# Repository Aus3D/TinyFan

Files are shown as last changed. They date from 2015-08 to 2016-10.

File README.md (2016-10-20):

# TinyFan

TinyFan is an fan expansion board for the RAMPS 3D printer control board. It allows control of two additional fans through pins D6 and D11.

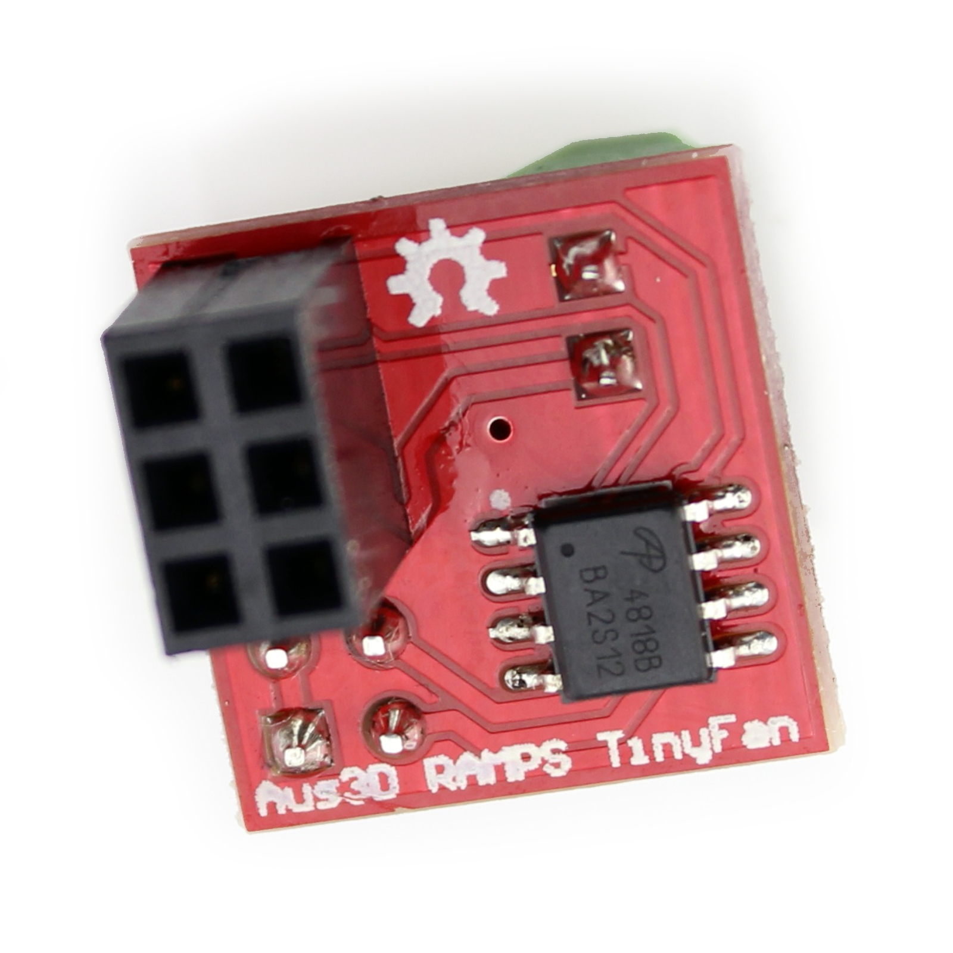
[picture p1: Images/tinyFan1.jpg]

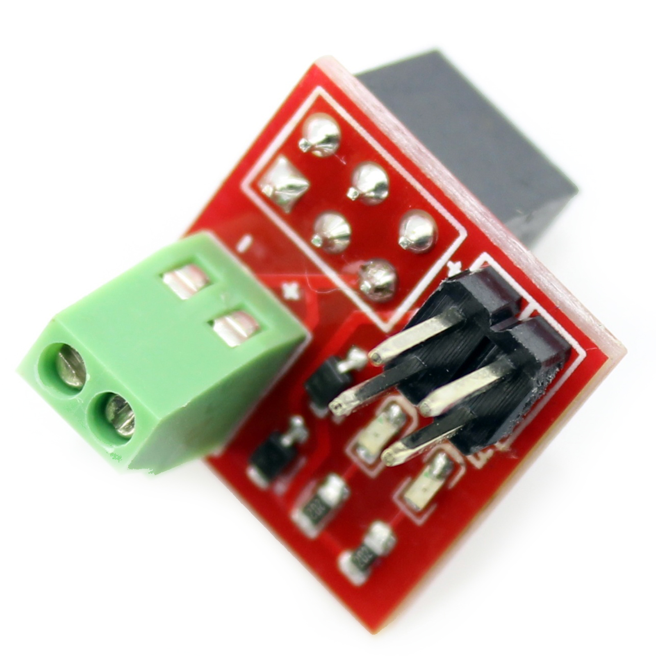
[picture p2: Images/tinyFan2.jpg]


TinyFan is designed to be easy to install. It plugs directly into RAMPS - no soldering is required. A screw terminal allows for connection to 12/24V, so two short wires can be run from RAMPS power input screw terminals to the TinyFan board. This also allows TinyFan to operate at a different voltage to the main power supplied to RAMPS.

Standard .1" pin headers are used for fan connections.

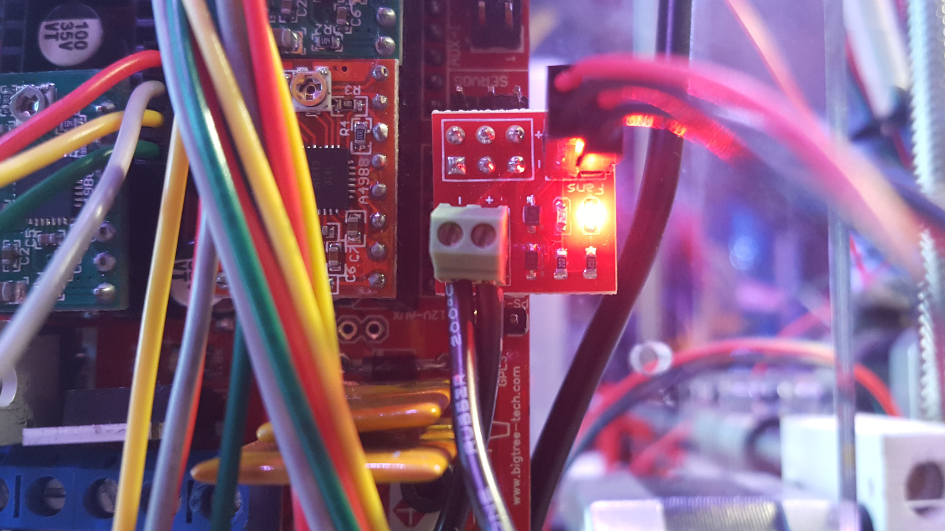
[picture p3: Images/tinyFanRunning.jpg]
TinyFan Running


For more information on TinyFan, including a guide for Marlin firmware configuration, check the [Aus3D Wiki](http://wiki.aus3d.com.au/index.php?title=TinyFan).

TinyFan is open source, and licensed under the GPL V3. TinyFan was designed in Altium Designer, which may make it difficult for some to access - gerber files (for manufacturing) and PDF files (for schematic) have been included to attempt to address this.

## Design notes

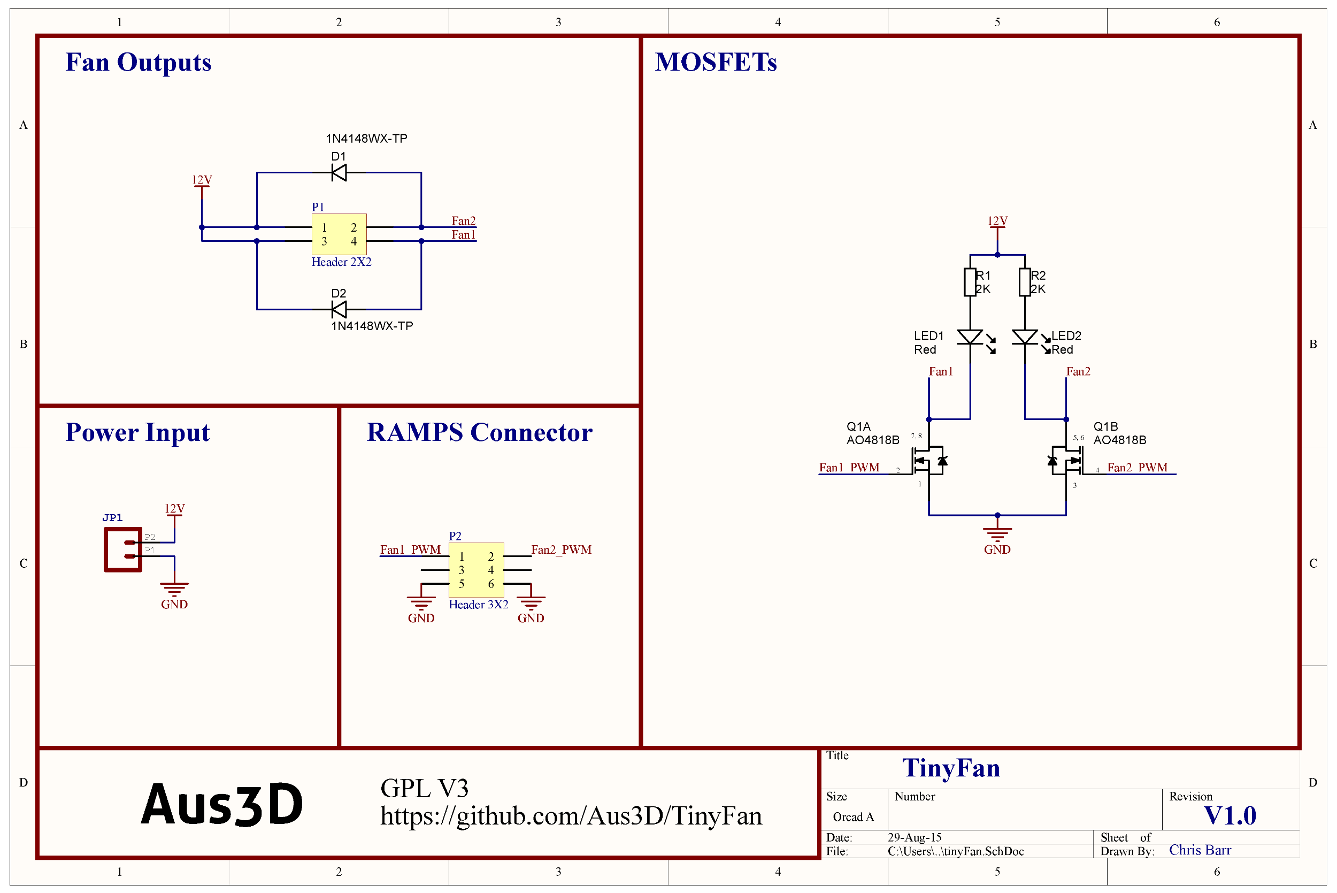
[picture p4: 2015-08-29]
Images/schematic.png

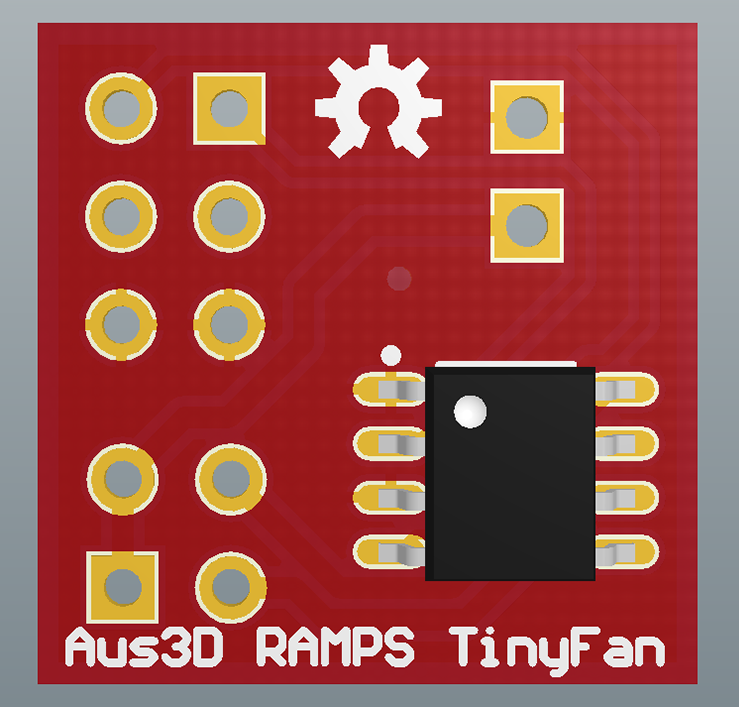
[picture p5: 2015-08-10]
Images/preview2.PNG

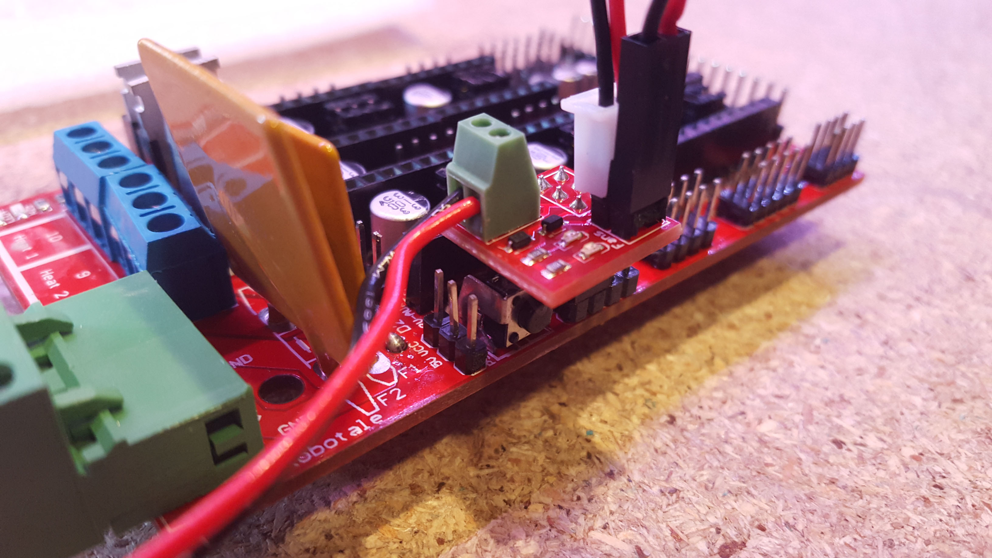
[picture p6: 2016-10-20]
Images/tinyFanConnected2.jpg

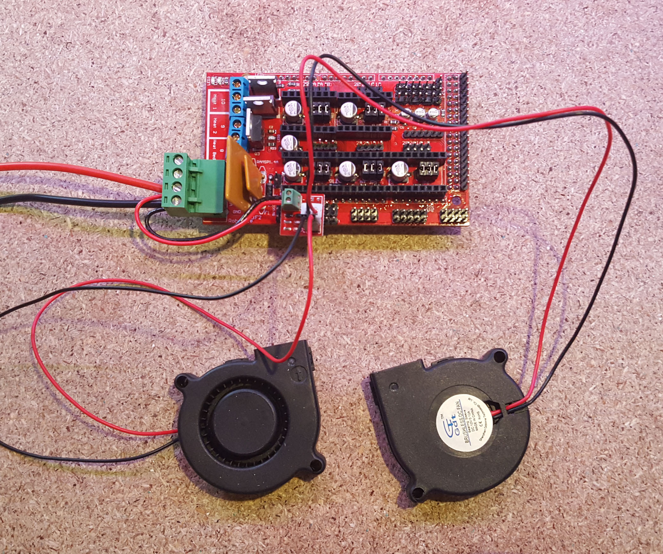
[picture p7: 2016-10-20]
Images/tinyFanConnected.jpg

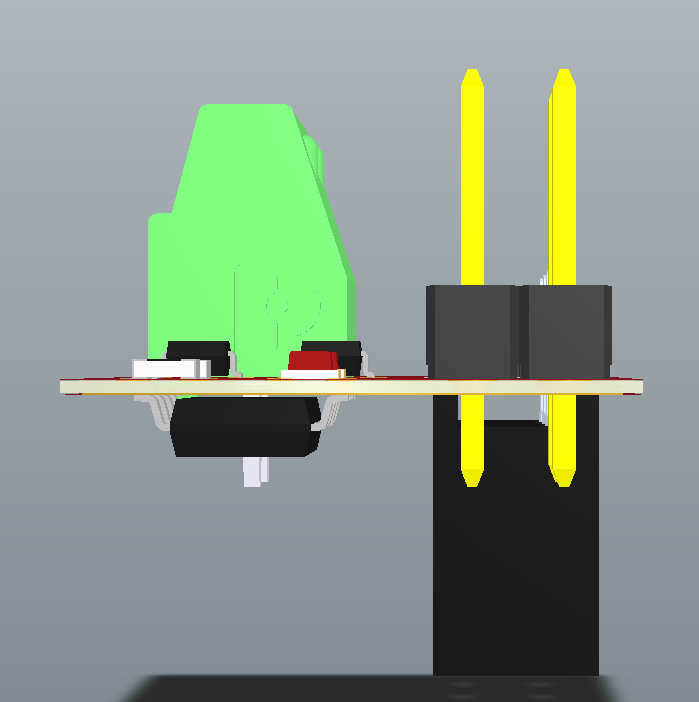
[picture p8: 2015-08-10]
Images/preview3.PNG

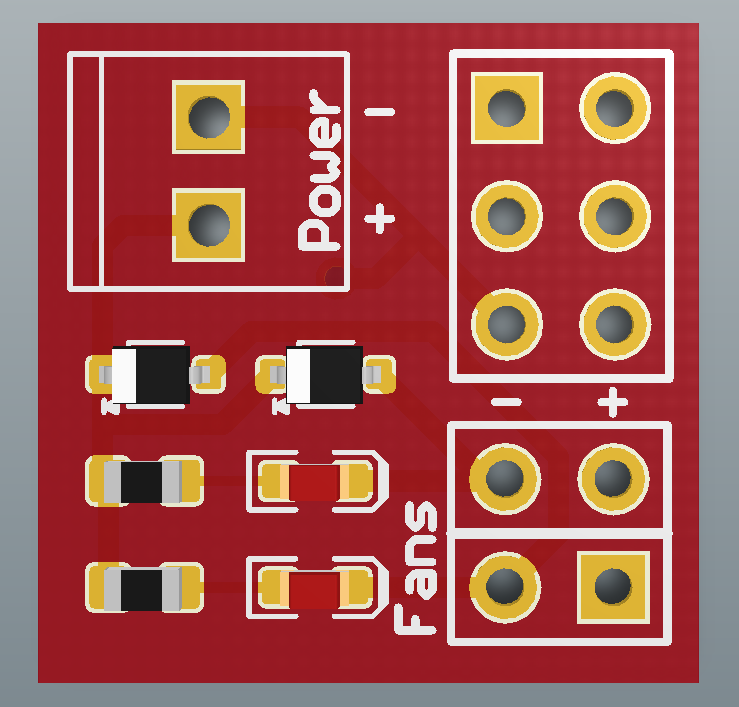
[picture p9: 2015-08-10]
Images/preview.PNG

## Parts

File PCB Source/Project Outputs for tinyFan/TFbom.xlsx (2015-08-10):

Designator | Manufacturer | Part Number | Digikey Part Number | Comment | Description | Footprint | Quantity
D1, D2 | DiodesZetex | 1N4448WS-7-F | 1N4448WS-FDICT-ND | DIODE_75V_500mW | Diode SMD 300mA 0.5W SOD323 | SOD323 | 2
JP1 | On Shore Technology Inc | OSTVN02A150 | ED10561-ND | Any matching screw terminal suitable | 2.54mm 2-pin Screw Terminal | 1X02_2.54_SCREWTERM | 1
LED1, LED2 | Kingbright | APT1608SURCK | 754-1123-1-ND | Red | LED 0603 SMD Hyper Red 630nm 220mcd 20mA | LED-0603-RED | 2
P1 | FCI | 67997-404HLF | 609-3242-ND | Header 2X2 Male | Header, 2-Pin, Dual row | HDR2X2 | 1
P2 | Sullins Connector Solutions | PPTC032LFBN-RC | S7071-ND | Header 3X2 Female | Header, 3-Pin, Dual row | HDR2X3 | 1
Q1 | Alpha & Omega Semiconductor Inc | AO4818B | 785-1059-1-ND | MOSFET_AO4818B | MOSFET Dual-Channel 30V 8.5A SOIC-8 SMD | SOIC127P600X175-8AN | 1
R1, R2 | Yageo | RC0603FR-072KL | 311-2.00KHRCT-ND | Any Thick Film 2K 0603 0.1W 5% Resistor Suitable | Resistor SMD chip 2K Ohm 0.1W 5% 0603 | RESC1608X55N | 2

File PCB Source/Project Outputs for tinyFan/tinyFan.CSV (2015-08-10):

Bill of Material for
On 09-Aug-15 at 10:15:59 PM
Comment | Pattern | Quantity | Components
Comment | OSHW-LOGO-S | 1 | Designator25
DIODE_75V_500mW | SOD323 | 2 | D1, D2 | Diode SMD 300mA 0.5W SOD323
Header 2X2 | HDR2X2 | 1 | P1 | Header, 2-Pin, Dual row
Header 3X2 | HDR2X3 | 1 | P2 | Header, 3-Pin, Dual row
MOSFET_AO4818B | SOIC127P600X175-8AN | 1 | Q1 | MOSFET Dual-Channel 30V 8.5A SOIC-8 SMD
Red | LED-0603-RED | 2 | LED1, LED2 | LED 0603 SMD Hyper Red 630nm 220mcd 20mA
Standard 2-pin 0.1 header. Use with - straight break away headers ( PRT-00116) - right angle break away headers (PRT-00553) - swiss pins (PRT-00743) - machine pins (PRT-00117) - female headers (PRT-00115) Molex polarized connector foot print use with: PRT-08233 with associated crimp pins and housings. 2.54_SCREWTERM for use with PRT-10571. 3.5mm Screw Terminal footprints for PRT-08084 5mm Screw Terminal footprints for use with PRT-08432" | 1X02_2.54_SCREWTERM | 1 | JP1
Thick Film | RESC1608X55N | 2 | R1, R2 | Resistor SMD chip 330 Ohm 0.1W 5% 0603

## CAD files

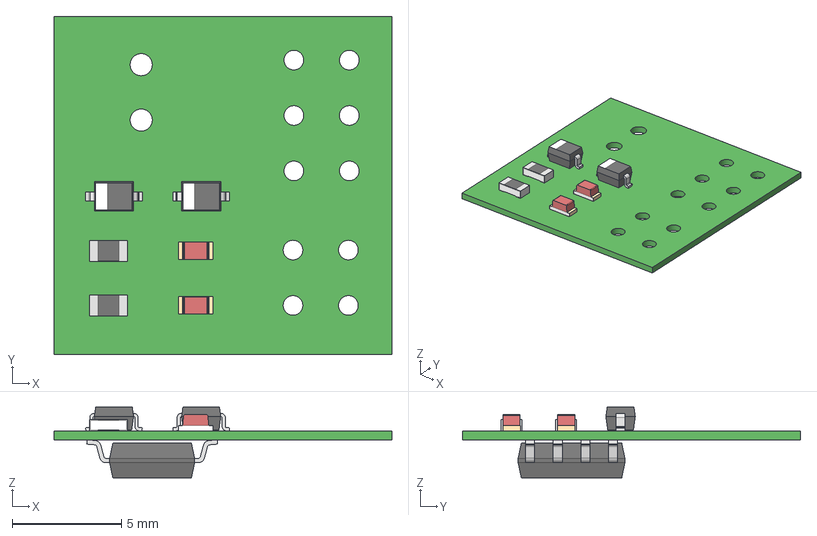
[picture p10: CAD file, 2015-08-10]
3D Model/tinyFan.step
15.5 x 15.5 x 3.25 mm
Board
SOD323 x 2
RES_0603_(1608_metric) x 2
LED_0603_APT1608_RED x 2
SOIC-8

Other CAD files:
3D Model/D1.sldasm
3D Model/LED1.sldasm
3D Model/Q1.sldasm
3D Model/D2.sldasm
3D Model/R2.sldasm
3D Model/R1.sldasm
3D Model/LED2.sldasm
3D Model/LED_0603_APT1608_RED.sldprt
3D Model/Board.sldprt
3D Model/SOIC-8.sldprt
3D Model/SOD323.sldprt
3D Model/RES_0603_(1608_metric).sldprt
3D Model/tinyFan.SLDASM

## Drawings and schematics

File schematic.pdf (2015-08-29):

Fan Outputs | MOSFETs

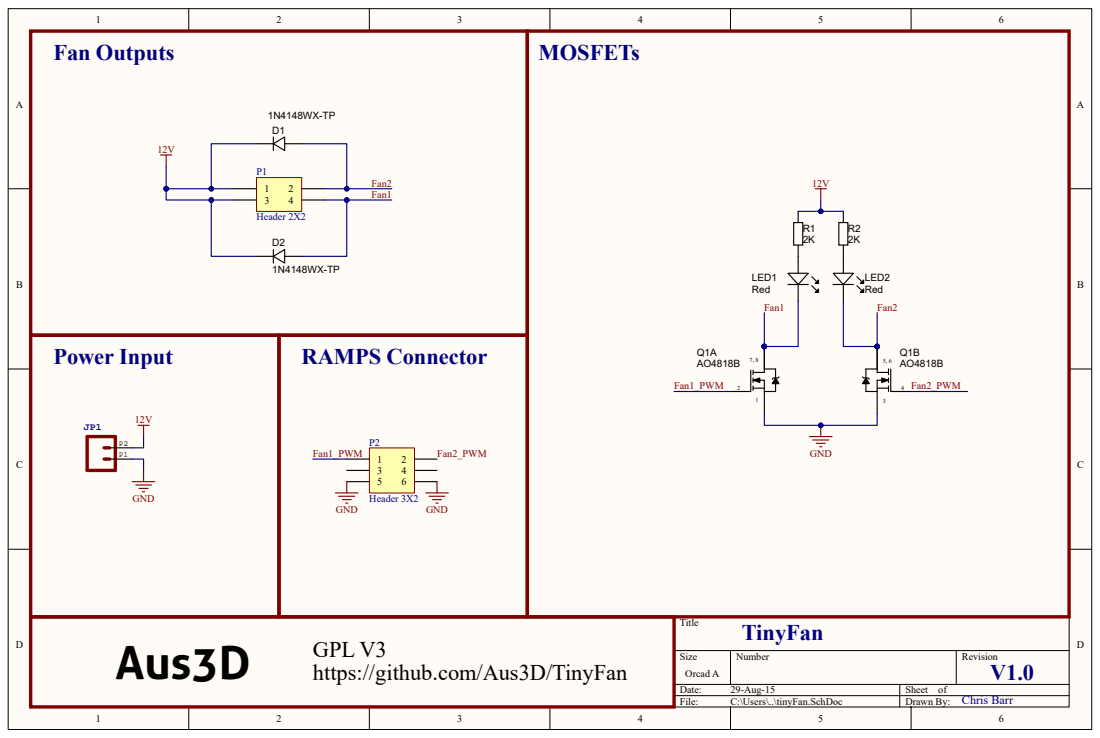
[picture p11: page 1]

Aus3D GPL V3 https://github.com/Aus3D/TinyFan | Title TinyFan
Size Orcad A | Number | V1.0 Revision

Date: 29-Aug-15 | Sheet of
File: C:\Users\..\tinyFan.SchDoc | Drawn By: Chris Barr

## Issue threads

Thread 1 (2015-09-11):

Swap Vin Terminals?

chrissbarr, 2015-09-11:
Swapping polarity of Vin terminals would make them consistent with RAMPS power inputs - possibly more intuitive for wiring?

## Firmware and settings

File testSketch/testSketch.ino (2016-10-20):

/*
 *  TinyFan / MightyFan test sketch
 *  
 *  Upload sketch to Arduino Mega and connect fan board. 
 *  Supply fan board with power via screw terminals.
 *  Each LED on the board should turn light up in sequence.
 *  
 */

#define FAN_PIN_0   11    //tinyfan1    +   mightyfan1
#define FAN_PIN_1   6     //tinyfan2    +   mightyfan2
#define FAN_PIN_2   5     //                mightyfan3
#define FAN_PIN_3   4     //                mightyfan4

//uncomment MIGHTYFAN define to test MightyFan board
//#define MIGHTYFAN

#ifdef MIGHTYFAN
  #define FAN_NUM 4
#else
  #define FAN_NUM 2
#endif

byte fanPins[] = {FAN_PIN_0, FAN_PIN_1, FAN_PIN_2, FAN_PIN_3};

void setup() {

  for(int i = 0; i < FAN_NUM; i++) {
    pinMode(fanPins[i], OUTPUT);
  }

}

void loop() {

  for(int i = 0; i < FAN_NUM; i++) {

    //set all pins to low
    for(int j = 0; j < FAN_NUM; j++) {
      digitalWrite(fanPins[j], LOW);
    }

    //set current pin high
    digitalWrite(fanPins[i], HIGH);
    
    delay(1000);
  }

}

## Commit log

2015-08-10 Initial Commit
    Moving files from MK2 development repository.
    [Board.sldprt, D1.sldasm, D2.sldasm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]
2015-08-10 Added PDF Schematic
    Organised schematic, created PDF version.
    [tinyFan.PcbDoc, tinyFan.PrjPCB, tinyFan.SchDoc]
2015-08-10 Updated Images
    [tinyFan.PcbDoc, tinyFan.SchDoc]
2015-08-29 Schematic
    Added PNG Schematic. Updated PCB to show board size.
    [tinyFan.PcbDoc, tinyFan.SchDoc]
2015-08-29 Update Schematic
    Added logo, link to GitHub, license
    [tinyFan.SchDoc]
2015-08-29 Schematic Update
2015-08-29 Resized Schematic PNG
2015-08-29 Added PCB image
2015-10-24 Added old files
    [AFC.PrjPCB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]
2016-10-20 Tidying
    Change folder structure
    [AFC.PrjPCB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]
